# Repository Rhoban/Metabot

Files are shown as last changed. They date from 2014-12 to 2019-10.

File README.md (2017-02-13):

# The Metabot open-source quadruped robot

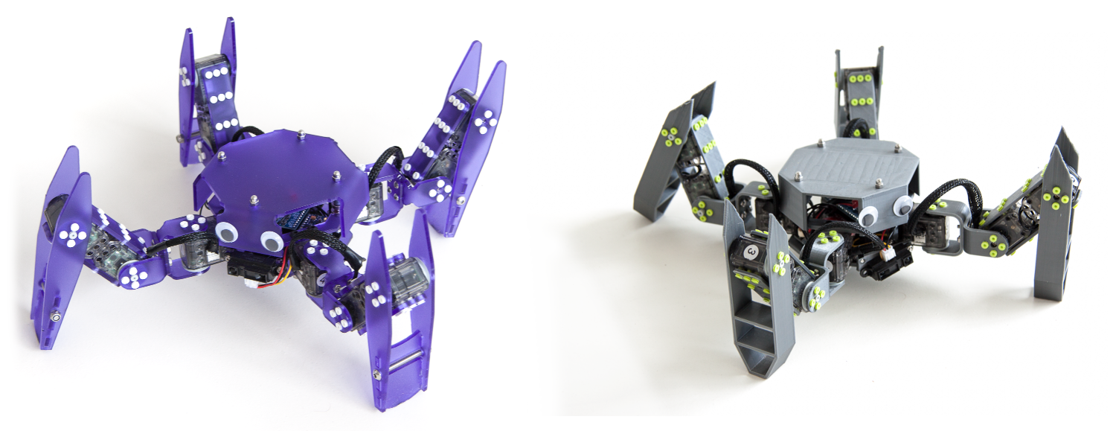
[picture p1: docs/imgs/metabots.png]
Metabot


Metabot is an open-source DIY quadruped robotics platform. It can be 3D printed or
laser cutted (3mm acrylic).

Note that [the robot is now available as a kit](http://metabot.cc).
In this repository you will find all the open-source material to make (or hack) your own.

* [Bill of material](docs/bom.md)
* Mechanics
    * [3D Parts](mechanics/3d)
    * [Laser parts](mechanics/laser)
* [Electronics](electronics)
* [Firmware](firmware)
* [Joypad firmware](dfpad)

You can control the robot using the Metabot app (available on the Play Store)

[To get information about the previous robot version, see branch V1](https://github.com/Rhoban/Metabot/tree/v1)

## License

This project is under CC BY-NC license:
http://creativecommons.org/licenses/by-nc/3.0/

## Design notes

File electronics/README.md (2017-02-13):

# Metabot electronics

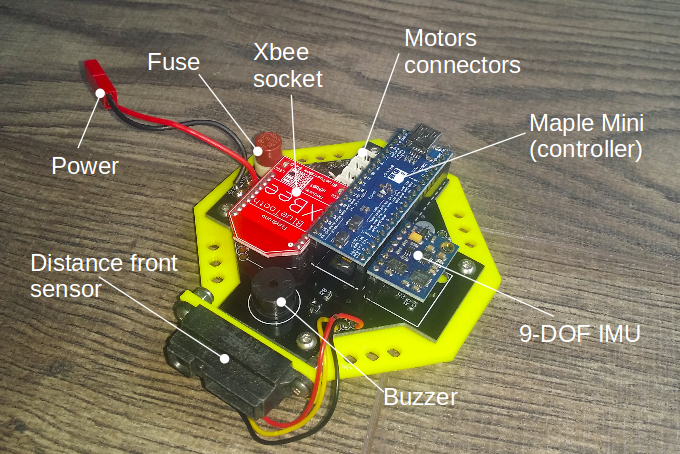
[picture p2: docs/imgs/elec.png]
Electronics


Here are eagle schematics of the XBoard, the electronics inside the Metabot
robot.

## BOM

To assemble the board, you'll need the following components:

Name       | Farnell       | Quantity      | Description
-----------|---------------|---------------|--------------------------------------
MOLEX-53253-0370 | 1756921 | 4 | Connector for the motors
CD74HCT367M | 1739593 | 1 | Bus driver
1x20 0.1" header | 1593469 | 2 | Connector for the maple mini
1x8 0.1" header | 1593463 | 1 | Connector for the IMU
1x10 1mm header | 1109732 | 2 | Connector for the XBee
CEM-1203 | - | 1 | Buzzer
BC817 | 1081223RL | 1 | NPN transistor for the buzzer
EEE1CA470SP | 9696946 | 1 | 47uF decoupling capacitor
EEEFK1C221XP | 1850103 | 1 | 220uF decoupling capacitor
TS2940CW-3.3RP | 7261403RL | 1             | 3.3V Regulator
AP1117E50G-13 | 1825292RL  | 1             | 5V Regulator
LITTELFUSE  56000001009  | 1185363 | 1     | Fuse holder
Radial Fuse, 3.15A  37013150410 | 1716619 | 1 | Fuse
SUD50N04-8M8P-4GE3 | 1794799 | 1     | This big MOS can blow up the fuse programmatically
JST-BEC connector | - | 1 | Connector for the battery
R0805 22 ohms | - | 2 | 
R0805 470 ohms | - | 2 | 
R0805 1 Kohms | - | 1 |
R0805 4 Kohms | - | 3 |
R0805 10 Kohms | - | 1 |
R0805 20 Kohms | - | 1 |
C0805 100nF | - | 1 |

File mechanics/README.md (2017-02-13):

# Mechanics

Here are the mechanics parts, [documentation can be found here](/doc/bom.md)

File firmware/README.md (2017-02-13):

# Firmware

The firmware is the code that is loaded on the robot and that generates the
walking gait and talks to the motors. It is currently only adapted for the
original 12-dof Metabot (4 legs, 3 motors per leg).

## Putting the firmware on the robot

### Linux

You need to install the following packets:

```
$ apt-get install python python-serial
```

To put the firmware on the robot, simply cd into the `firmware/` repository and
run the installation script:

```
sudo python robotis-loader.py /dev/ttyACM0 metabot2.bin
```

This should reset the board and then output some progress bar, your firmware is now
on the robot!

### Windows

You'll need python and pyserial. Then, be sure to have the drivers. You can install
simply OpenCM IDE for that.

Then, run:

```
sudo python robotis-loader.py COM4 metabot2.bin
```

Replace COM4 with the right serial port (you can see it in OpenCM ide or in the devices
manager).

## The terminal

### Connecting to the on-board terminal

#### Linux

You can open a serial connection with the robot using `cu` or `screen`. You can use
for instance:

```
you@yourmachine: cu -l /dev/ttyACM0
Connected.

$  
```

Type "~." to quit cu.

#### Windows

On Windows, you can use a serial client such as PuTTy. Just choose "Serial" as connection
mode and enter "COMx", where x is the number of the device.

You can find the number of the device in the devices manager.

## Commands

### Basics

#### `start`: Enable the motors

This will enable the motors. The LEDs will turn green and the torque will rise
slowly until the robot reaches it default position.

#### `stop`: Stop the motors

Turns the LEDs red and shuts the torque down.

#### `beep [freq] [duration]`: Emit a beep

This will emit a beep using the internal buzzer, using `freq` Hz and `duration`
ms.

### Controller

Here are commands that can be used to control the motion of the robot

#### `dx`, `dy`, `turn`: Controls the robot

These are parameters that control the robot speed. Actually, `dx` and `dy`
control the size of the each step (in mm) and `turn` the angle of each step
(in °).

#### `freq`: Steps per second

This is the number of step the robot does on each second.

#### `h`: Robot height

This is the (z, in mm) height of the robot while it walks.

#### `r`: Radius

This is the radius of the legs (in mm), i.e the distance of the legs to the
center of the body while walking.

#### `alt`: Legs altitude

This parameters controls the height the legs are lifted up (in mm) while
walking.

#### `crab`: Crab position

This is an angle (in °) that can be positive or negative and allows to get a
crab-like position while walking.

## Building, developing & hacking the firmware

See the [firmware source README](src#firmware-source)

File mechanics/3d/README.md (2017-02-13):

# Mechanics

Here are the 3D mechanics parts, [documentation can be found here](/docs/bom.md)

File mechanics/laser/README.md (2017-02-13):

# Mechanics

Here are the laser mechanics parts, [documentation can be found here](/docs/bom.md)

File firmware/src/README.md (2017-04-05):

# Firmware source

## Building, developing & hacking the firmware

See the [firmware source](src/README.md)

You should install the arm cross-compilation toolchain:

```
sudo apt-get install libstdc++-arm-none-eabi-newlib gcc-arm-none-eabi libnewlib-arm-none-eabi binutils-arm-none-eabi
```

The firmware source is in the `src/` directory. To build it, you'll first have to run the
prepare script to get the Maple framework:

```
./prepare.sh
```

Then, run `make`:

```
make
```

You can use `make install` to send directly the firmware on the robot:

```
make install
```

## Creating behaviors

We already designed a simple architecture with few examples that can be found in the
firmware in order to create behaviors for the robot.

First, edit `behavior.h` and change the `BEHAVIOR_ENABLE` constant to `1`. Then, edit
`behavior.cpp`, you can read the examples functions and uncomment the one(s) you like
in the `behavior_tick` method.

This will be executed when the robot is started (i.e when the `start` command is sent and
after the motors are enabled). Feel free to edit this to create your own, custom behavior.

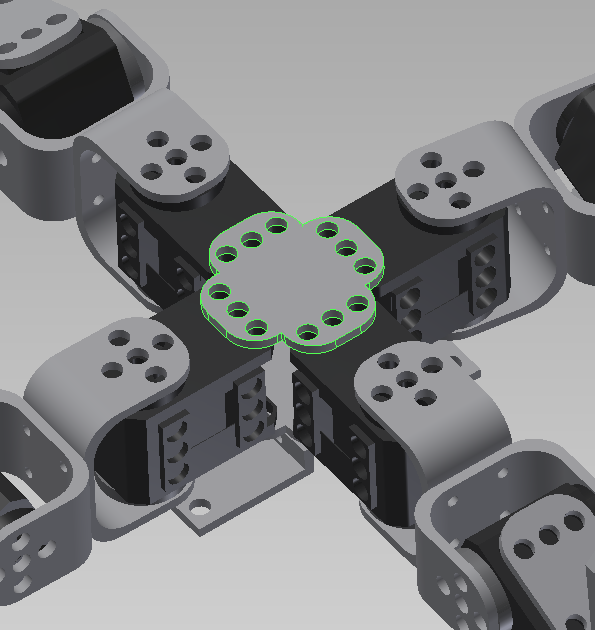
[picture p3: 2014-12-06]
mechanics/3d/imgs/body.png

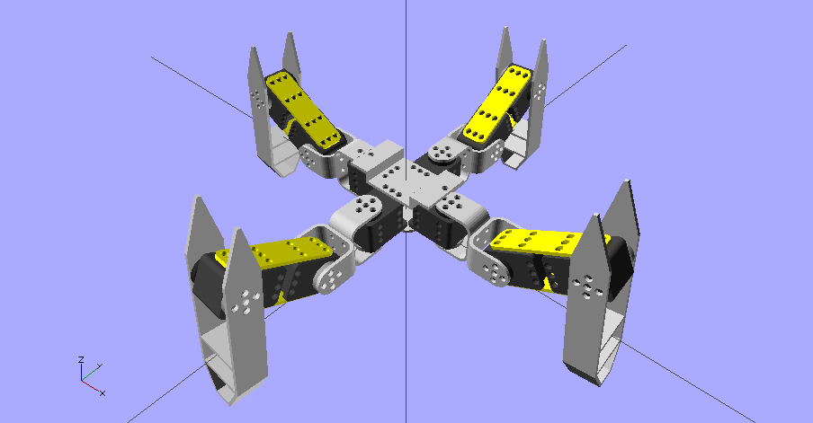
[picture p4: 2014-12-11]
mechanics/3d/imgs/side.png

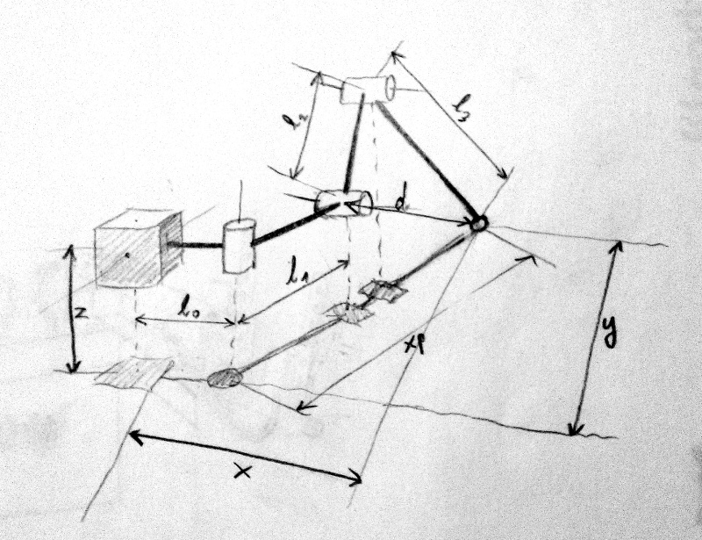
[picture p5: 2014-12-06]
docs/imgs/kinematic.jpg

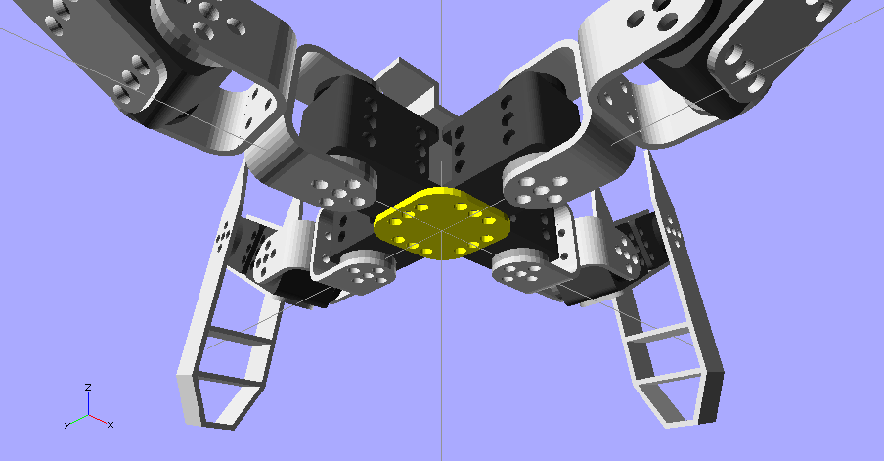
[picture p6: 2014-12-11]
mechanics/3d/imgs/body_bottom.png

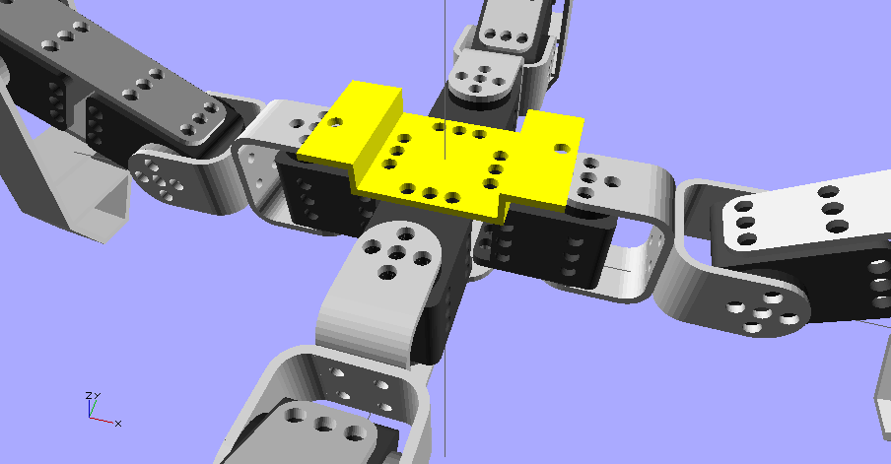
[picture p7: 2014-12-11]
mechanics/3d/imgs/body_top.png

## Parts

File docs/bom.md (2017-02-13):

# Bill of material

Metabot V2 bill of materials

## ROBOTIS parts

Name                   | Quantity | Description                  
-----------------------|----------|----------------------------------
XL-320                 | 12       | Robot servo-motors
Short Rivets           | ~300     | Short rivets
Long Rivets            | 48       | Long rivets
Ollo Pulley            | 12       | The pulley for the counter-axis
Ollo Tool              | 1        | A plastic tool that can be used to handle rivets

## Electronics

Name                   | Quantity | Description                  
-----------------------|----------|----------------------------------
XBoard                 | 1        | This is the custom [board](/electronics/) of the robot
Maple Mini             | 1        | A controller featuring a STM32F103CBT6, with sockets
Mini USB cable         | 1        | You'll need it to connect to the Maple Mini
GY-85 IMU              | 1        | 9DOF inertial measurement units (accelerometer, gyroscope and magnetometer)
XBee Bluetooth         | 1        | You can actually choose any bluetooth chip you want
GP2Y0A21YK             | 1        | 10 to 80 cm infrared distance sensor

## Batteries

The XBoard features a JST-BEC female connector, which is compatible with many LiPo battery.
You can actually use a lot of different power sources, but we recommend you the following references:

Name                   | Quantity | Description                  
-----------------------|----------|----------------------------------
1000mAh 2S (7.4) LiPo  | 1        | A battery, be careful about its geometry
IMAX B3 AC charger     | 1        | A cheap and simple to use LiPo charger

## Mechanics

Name                   | Quantity | Description                  
-----------------------|----------|----------------------------------
M4x40                  | 12        | Tie the leg tips and the body
M3x8                   | 7        | 4 for the magnets to the head, 1 for the IMU and 2 for the GP-2
M3x5 (countersunk)     | 4        | Used to tie the magnets to the spacers
M3 nylstop caps        | 16       | We recommend nylstop caps
M4 nylstop caps        | 12       | We recommend nylstop caps
M3 blind cap nut       | 4        | Blind caps are prettiest for the top of the head
Nylon M3 cap           | 17       | 8 for the electronics, 1 for the IMU, 2 for the GP-2, 4 for the body spacers, 2 to replace magnets (to avoid magnetic interference)
M3x12 male spacer      | 1        | For the IMU
M3x15ish male spacer      | 4        | For the electronics
M3x10                  | 20        | 16 for the Us, 4 for the electronics 
Countersunk magnet (10x3mm, 3mm hole) | 6        | To plug and unplug the head
Googly eyes            | 2        | You can paste it on the front on the robot to get it nicer

Note that you'll need allen 2 and 2.5, and a flat plier or an hex wrench for the nylstop caps

## Parts

For mechanical parts, you have choice between 3D and laser. You can either print the
parts yourself or cut it and bend it.

### The 3D option

Name                   | Quantity 
-----------------------|----------
[U](/mechanics/3d/u.stl) | 8      
[side](/mechanics/3d/side.stl) | 8
[leg](/mechanics/3d/leg.stl) | 4
[body_bottom](/mechanics/3d/body_bottom.stl) | 1
[body_top](/mechanics/3d/body_top.stl) | 1
[head](/mechanics/3d/head.stl) | 1

### The laser option

The parts are provided as DXF, the black layer (0) is cutting and the red one (1)
is 1mm engraving. The target material is 3mm thick PMMA (acrylic).

A packet version can also be [found here](/mechanics/laser/metabot.dxf).

Name                   | Quantity | Comment
-----------------------|----------|-------------
[U](/mechanics/laser/parts/u.dxf) | 8 | [Requires bending](/mechanics/laser/doc/u_bending.pdf)
[side](/mechanics/laser/parts/side.dxf) | 8 | 
[leg](/mechanics/laser/parts/leg.dxf) | 4 |
[tip](/mechanics/laser/parts/tip.dxf) | 4 |
[tip_up](/mechanics/laser/parts/tip_up.dxf) | 4 |
[body_bottom](/mechanics/laser/parts/body_bottom.dxf) | 1 | [Requires bending](/mechanics/laser/doc/body_bending.pdf)
[body_top](/mechanics/laser/parts/body_top.dxf) | 1
[head](/mechanics/laser/parts/head.dxf) | 1 | [Required bending](/mechanics/laser/doc/head_bending.pdf)

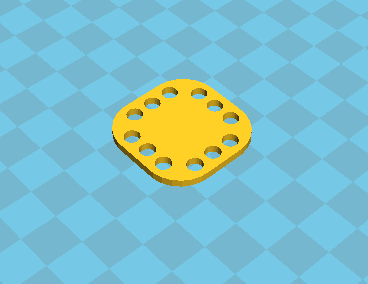
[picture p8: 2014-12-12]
mechanics/3d/imgs/parts/body_bottom.png

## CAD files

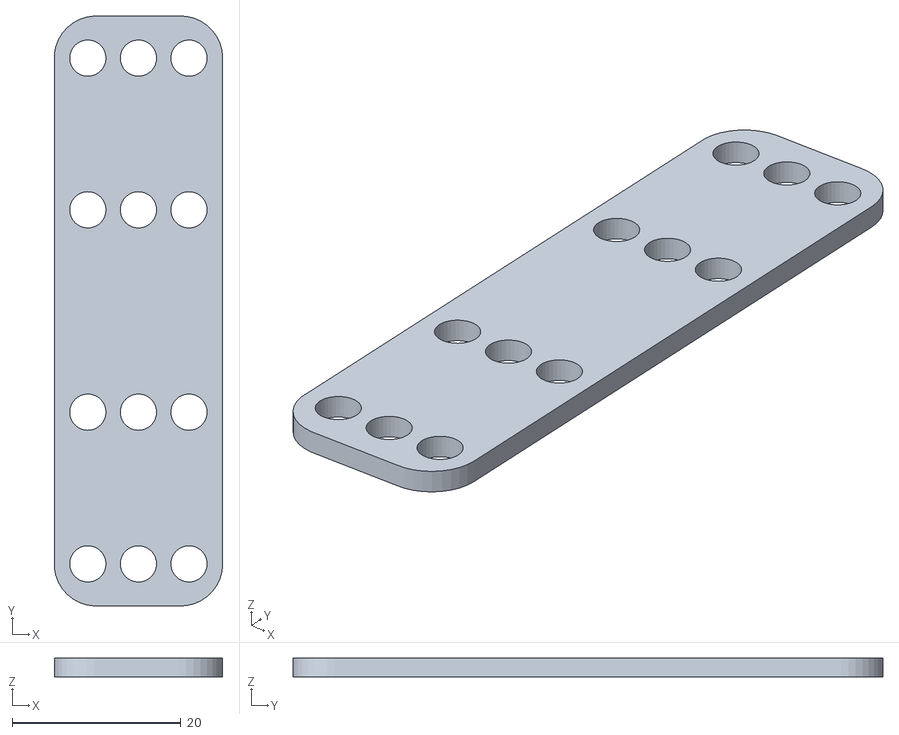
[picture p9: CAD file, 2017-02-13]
mechanics/3d/side.stl
20.0 x 70.0 x 2.20

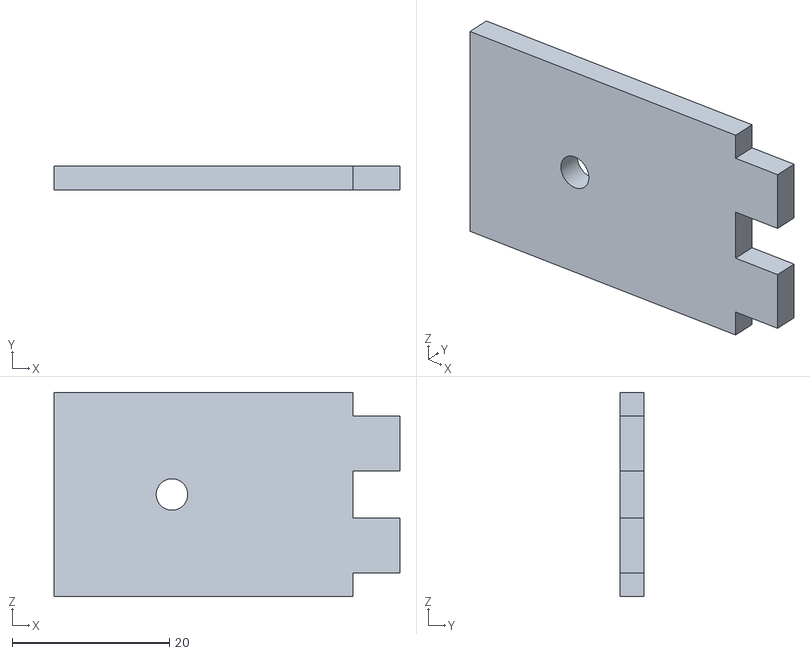
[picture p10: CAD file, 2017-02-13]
mechanics/laser/autodesk/u_pattern/u_side.stl
44.0 x 3.00 x 26.0

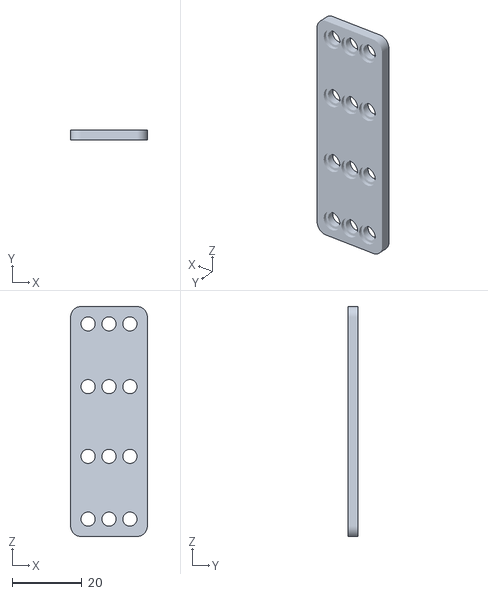
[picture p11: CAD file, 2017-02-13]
mechanics/laser/side.stl
22.0 x 3.00 x 66.0

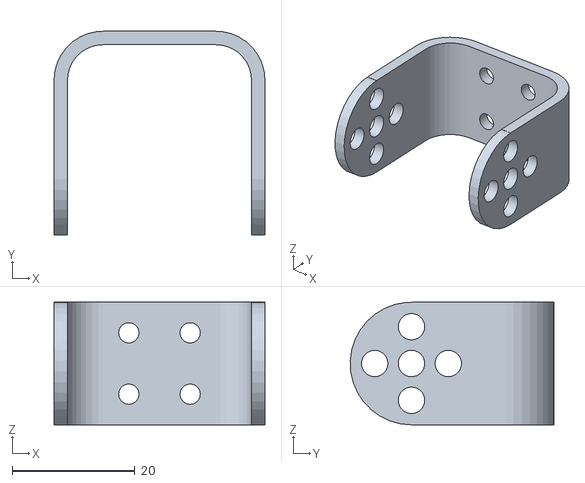
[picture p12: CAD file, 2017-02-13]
mechanics/3d/u.stl
34.4 x 33.2 x 20.0

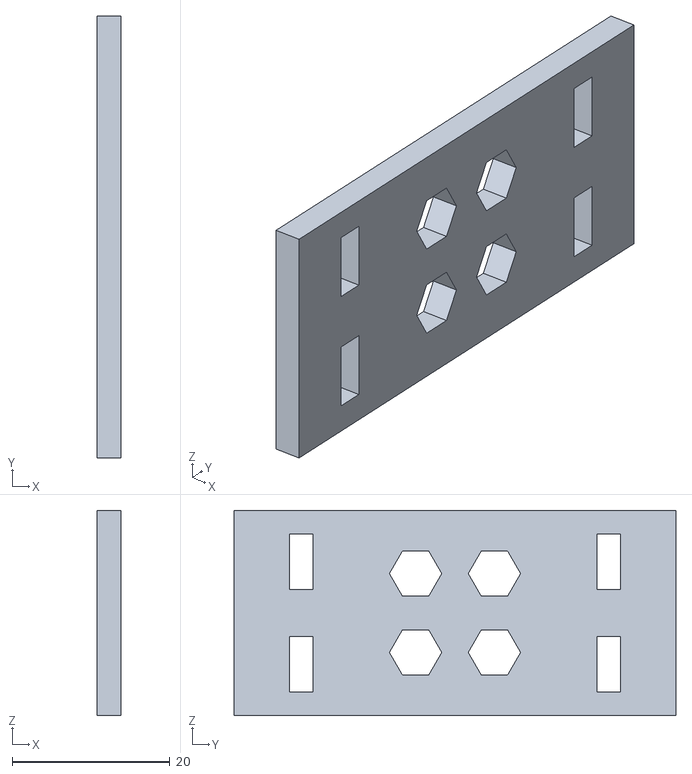
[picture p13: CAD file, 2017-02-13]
mechanics/laser/autodesk/u_pattern/u_base_hex.stl
3.00 x 56.0 x 26.0

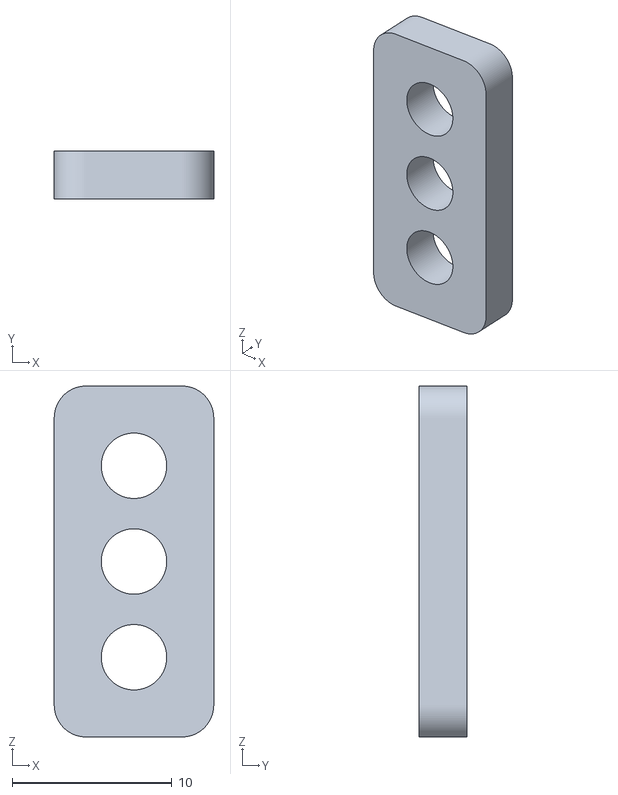
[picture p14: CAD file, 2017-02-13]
mechanics/laser/spacer.stl
10.0 x 3.00 x 22.0

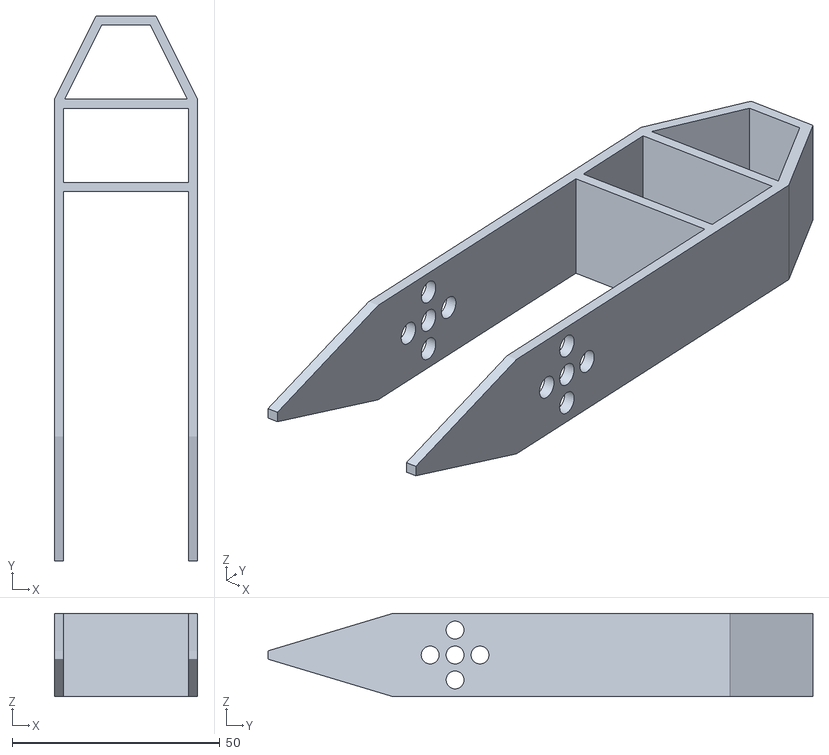
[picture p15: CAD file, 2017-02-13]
mechanics/3d/leg.stl
34.4 x 131.1 x 20.0

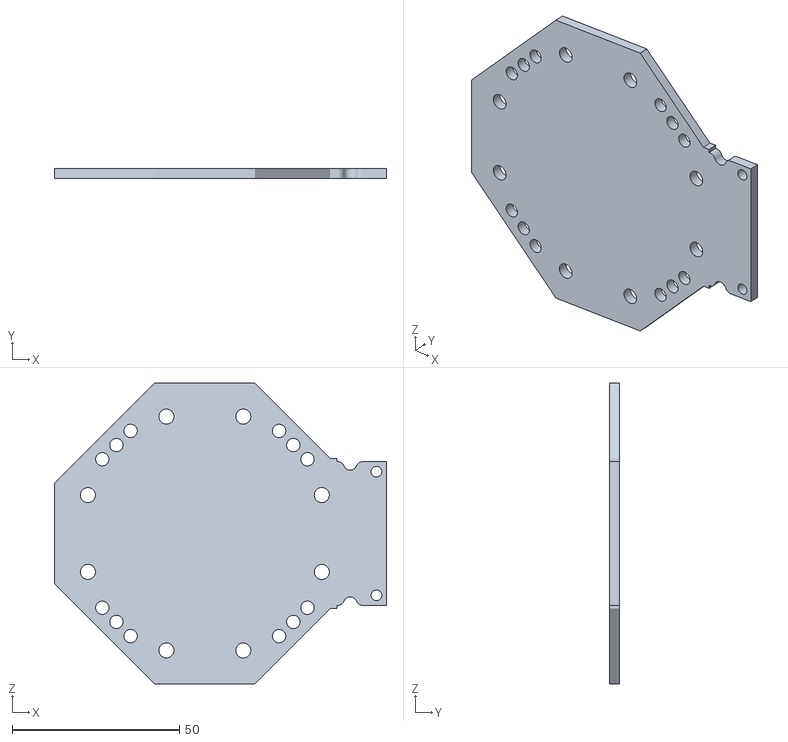
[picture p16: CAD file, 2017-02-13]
mechanics/laser/body_bottom.stl
99.4 x 3.00 x 90.0

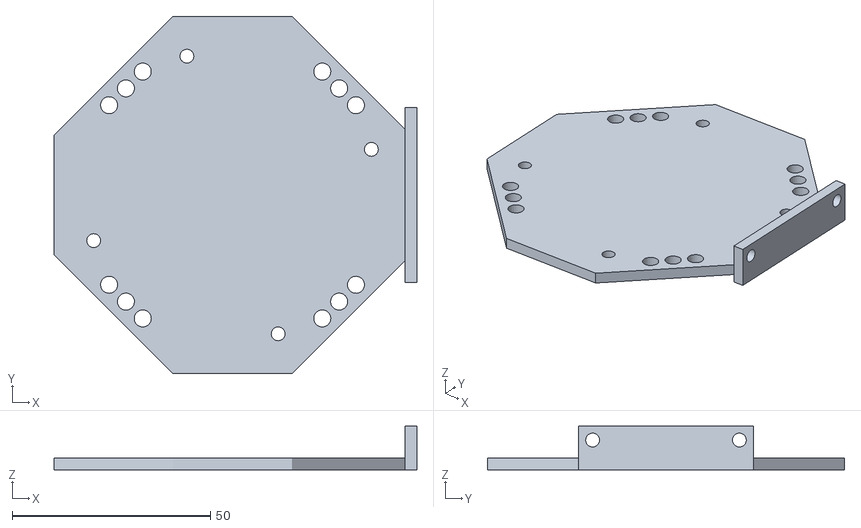
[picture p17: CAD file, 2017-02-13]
mechanics/3d/body_bottom.stl
91.5 x 90.0 x 11.0

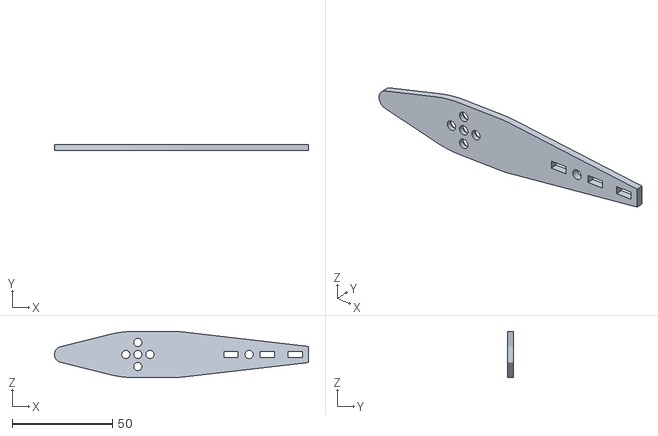
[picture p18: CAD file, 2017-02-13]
mechanics/laser/leg.stl
126.5 x 3.00 x 23.0

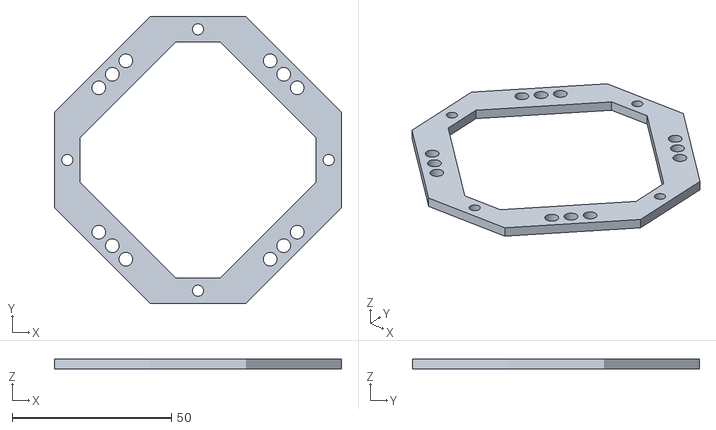
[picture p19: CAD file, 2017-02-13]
mechanics/3d/body_top.stl
90.0 x 90.0 x 3.00

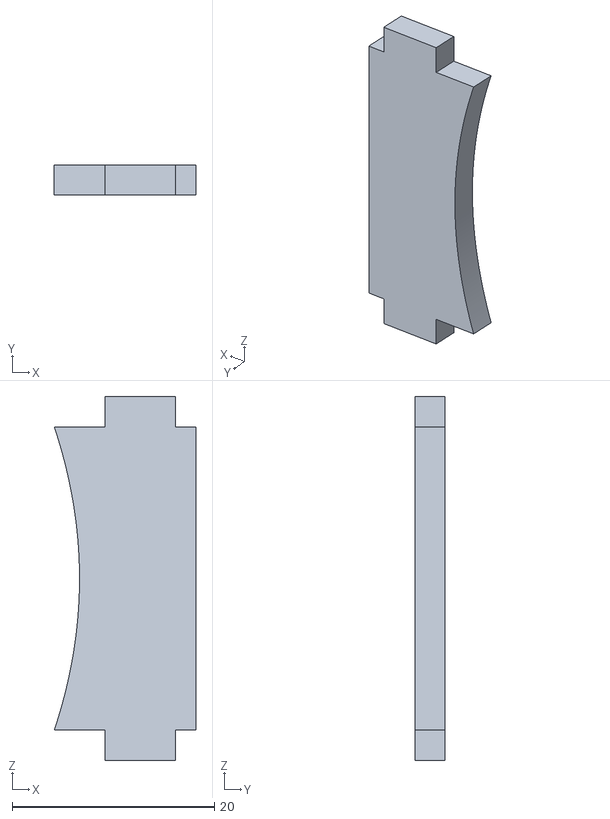
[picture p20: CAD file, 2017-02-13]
mechanics/laser/tip_up.stl
14.0 x 3.00 x 36.0

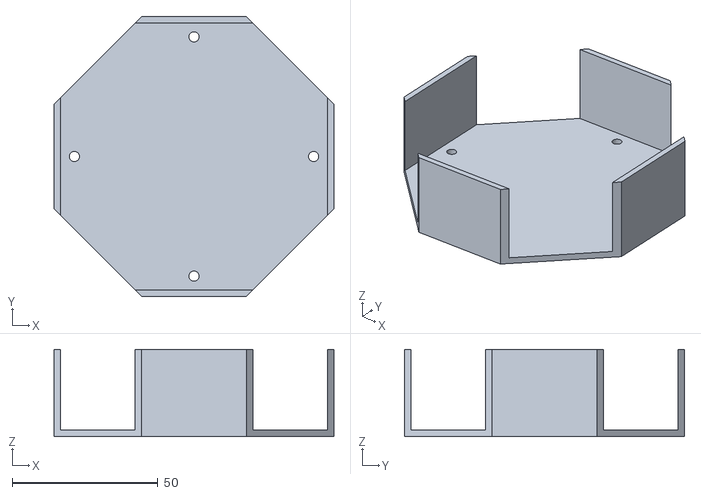
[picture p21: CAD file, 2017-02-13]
mechanics/3d/head.stl
96.0 x 96.0 x 30.0

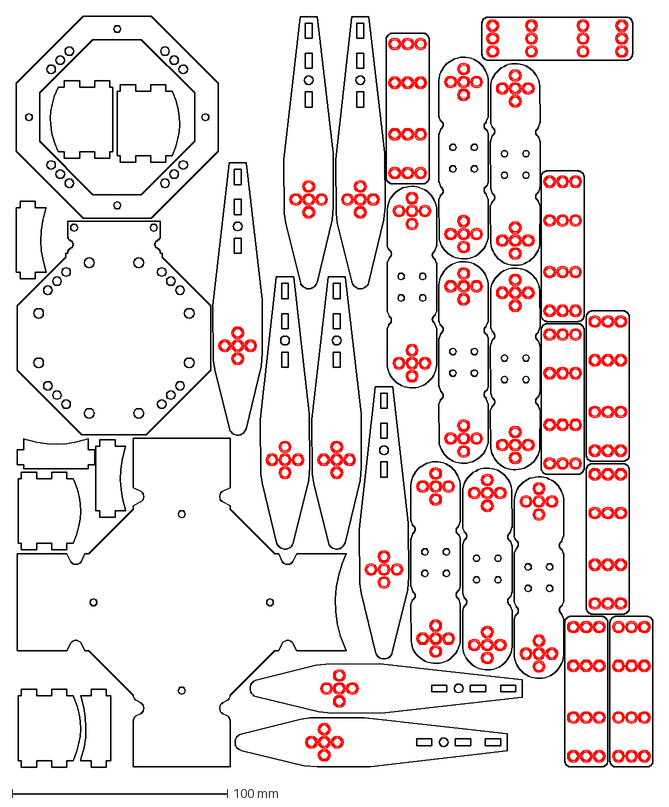
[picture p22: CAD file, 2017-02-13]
mechanics/laser/metabot.dxf
296.0 x 349.0 mm

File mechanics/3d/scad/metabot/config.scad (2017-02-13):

// Color of the parts, for rendering
PartsColor = [0.8, 0.8, 0.8];

// Head height
HeadHeight=30;

// Thickness of parts (2.2 is good for Ollo rivets)
Thickness = 2.2;
BodyThickness = 3;

// Sizes of the parts of the leg
// Ratio of leg parts
LegSize = 100;
LegSizeA = (0.60)*LegSize;
LegSizeB = (0.20)*LegSize;
LegSizeC = (0.20)*LegSize;

// Width of the bottom part of the leg
LegSizeBottom = 10;

// Size of the "top" part of the legs, in mm
LegSizeTop = 30;

// Motor dimensions
MotorWidth = 24;
MotorHeight = 36;
MotorDepth = 24;
MotorArmOffset = 9;

// U dimensions
UHeight = 15.2;
URadius = 8;
UWidth = 30+Thickness/2;
UTotalHeight = UHeight+URadius;
UScrewsSpacing = 10;
UScrewsDiameter= 3.3;

// Side dimensions
SideSize = 35;
SideHolesToBorder = 5;

// Defining the resolution
$fn=35;

module metabot_colorize() {
    color(PartsColor)
        children();
}

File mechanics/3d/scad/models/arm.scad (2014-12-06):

include <ollo.scad>;

module arm(counter=false) {
    c = counter?[0.6,0.6,0.6]:[0.15,0.15,0.15];
    color(c) {
        difference() {
            cylinder(d=20, h=OlloWidth);
            servoArm(OlloWidth);
        }
    }
}

arm();

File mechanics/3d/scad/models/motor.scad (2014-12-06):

include <ollo.scad>;
use <../util/rounded.scad>;

// Motor dimensions
MotorWidth = 24; 
MotorHeight = 36; 
MotorDepth = 24; 
MotorArmOffset = 9;

module motor(width=2.2) {
  translate([0,-MotorArmOffset,-MotorDepth/2]) {
  color([0.25,0.25,0.25]) {
	 difference() {
  	   rounded(MotorWidth,MotorHeight,MotorDepth,3,center=true);

		// Bottom
      translate([-MotorWidth/2-0.1,-MotorHeight/2-0.1,3])
	     cube([MotorWidth+0.2, 5.7, MotorDepth-6]);

		translate([0,-MotorHeight/2+3])
		  threeOllo(MotorDepth);

		// Motor shaft
	   translate([0, MotorArmOffset])
     	  olloHole(MotorDepth+5);

		// Side holes
		for (side=[-MotorWidth/2,MotorWidth/2-width]) {
		translate([side,9,MotorDepth/2]) {
		  rotate([0,90,0]) {
		   threeOllo();
			translate([0,-3*OlloSpacing,0])
			  threeOllo();
		  }
		}
		}
	 }
  }
	}
}

motor();

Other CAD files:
mechanics/laser/autodesk/robot.dwg
mechanics/laser/autodesk/u_pattern/u_base.stl
mechanics/laser/u.stl
mechanics/laser/head.stl
mechanics/3d/scad/models/motor_arm.scad
mechanics/3d/scad/joints/double_u.scad
mechanics/3d/scad/joints/side_to_side.scad
mechanics/3d/scad/metabot/joints.scad
mechanics/3d/scad/metabot/metabot.scad
mechanics/3d/scad/metabot/parts.scad
mechanics/3d/scad/metabot/print/body_bottom.scad
mechanics/3d/scad/metabot/print/body_projection.scad
mechanics/3d/scad/metabot/print/body_top.scad
mechanics/3d/scad/metabot/print/head.scad
mechanics/3d/scad/metabot/print/leg.scad
mechanics/3d/scad/metabot/print/leg_projection.scad
mechanics/3d/scad/metabot/print/side.scad
mechanics/3d/scad/metabot/print/side_projection.scad
mechanics/3d/scad/metabot/print/u.scad
mechanics/3d/scad/metabot/print/u_projection.scad
mechanics/3d/scad/models/ollo.scad
mechanics/3d/scad/parts/body.scad
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

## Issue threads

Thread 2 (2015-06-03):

bug de simulateur

theking391, 2015-06-03:
le simulateur ne me permet pas d'effectuer un rectangle de 1200 mm sur 2200mm . Le robot ne respecte pas les angles imposés il dévie de sa trajectoire a partir du second coté ( le 1er 22000mm)

Gregwar, 2015-06-03:
Bonjour,
Les trajectoires simulées ne sont en effet pas parfaites, mais cela sera encore pire dans la réalité
Le robot va glisser sur le sol, les moteurs auront du retard etc.

theking391, 2015-06-03:
c'est embêtant car je dois participer a un concours et si je ne peux pas m'entrainer sur le logiciel ni sur le robot cela me désavantage grandement .Auriez vous une astuce/idée de comment résoudre ce problèmes ??

Gregwar, 2015-06-03:
Vous ne devez de toutes façon pas miser sur le fait qur les trajectoires seront suivies parfaitement
Essayez de fermer les yeux et de faire un parcours: c'est le même probleproblème

theking391, 2015-06-03:
ah. alors on va essayer de se débrouiller merci pour les infos:)

Gregwar, 2015-06-03:
Avez vous vu la vidéo de tutoriel?

alexandremrnd, 2015-06-03:
Bonjour,
Je suis un ami de theking391 et nous travaillons ensemble sur ce projet et je vous confirme que nous avons regarder la vidéo de tutoriel mais même en suivant toutes les étapes notre carré ou rectangle (de n'importe quelle taille d'ailleurs) ne respecte pas les angles et les rend inférieurs à 90°.
 Merci à vous :)

Gregwar, 2015-06-03:
Ce qu'il faut savoir, c'est que le robot fait des mouvements qui devraient *théoriquement* donner 90° ou tant de milimètres, mais dans la pratique, un grand nombre de choses peuvent faire que ça ne marche pas
Il est impossible de faire des "parcours" précis sans capteurs (dans une prochaine version, le robot sera équipé de capteurs de distances) ni aucun retour d'information
C'est un peu comme si vous essayiez de faire un parcours les yeux fermés

alexandremrnd, 2015-06-04:
Merci à vous pour votre suivi de notre problème. Pour information, nous travaillons avec Madame Blanc pour le Robot Maker's Day.
A bientôt. :)

Closed 2015-12-14.

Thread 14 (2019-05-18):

build error

leelegend94, 2019-05-18:
Compiling failed while "[LD]        maple_mini.elf" with many errors like the followings:

build/./Maple/LibRhoban/commands.o: In function `start()':
/home/parallels/Workspace/rl/metabot_project/firmware/src/Maple/LibRhoban/commands.cpp:69: undefined reference to `dxl_flush()'
...

AndreasFWallin, 2019-05-29:
I have the same problem, both on Windows and Linux

leelegend94, 2019-06-05:
There are 2 source file not compiled by default, which is however crucial for Metabot...
Fix:
in firmware/src/Maple/LibRhoban/rules.mk
1. "ENABLE_DXL := no"  --> "ENABLE_DXL := yes"
2. uncomment "#cppSRCS_$(d) += servos.cpp"
3. have fun

Closed 2019-06-05.

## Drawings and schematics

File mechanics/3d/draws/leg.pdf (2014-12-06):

11

22

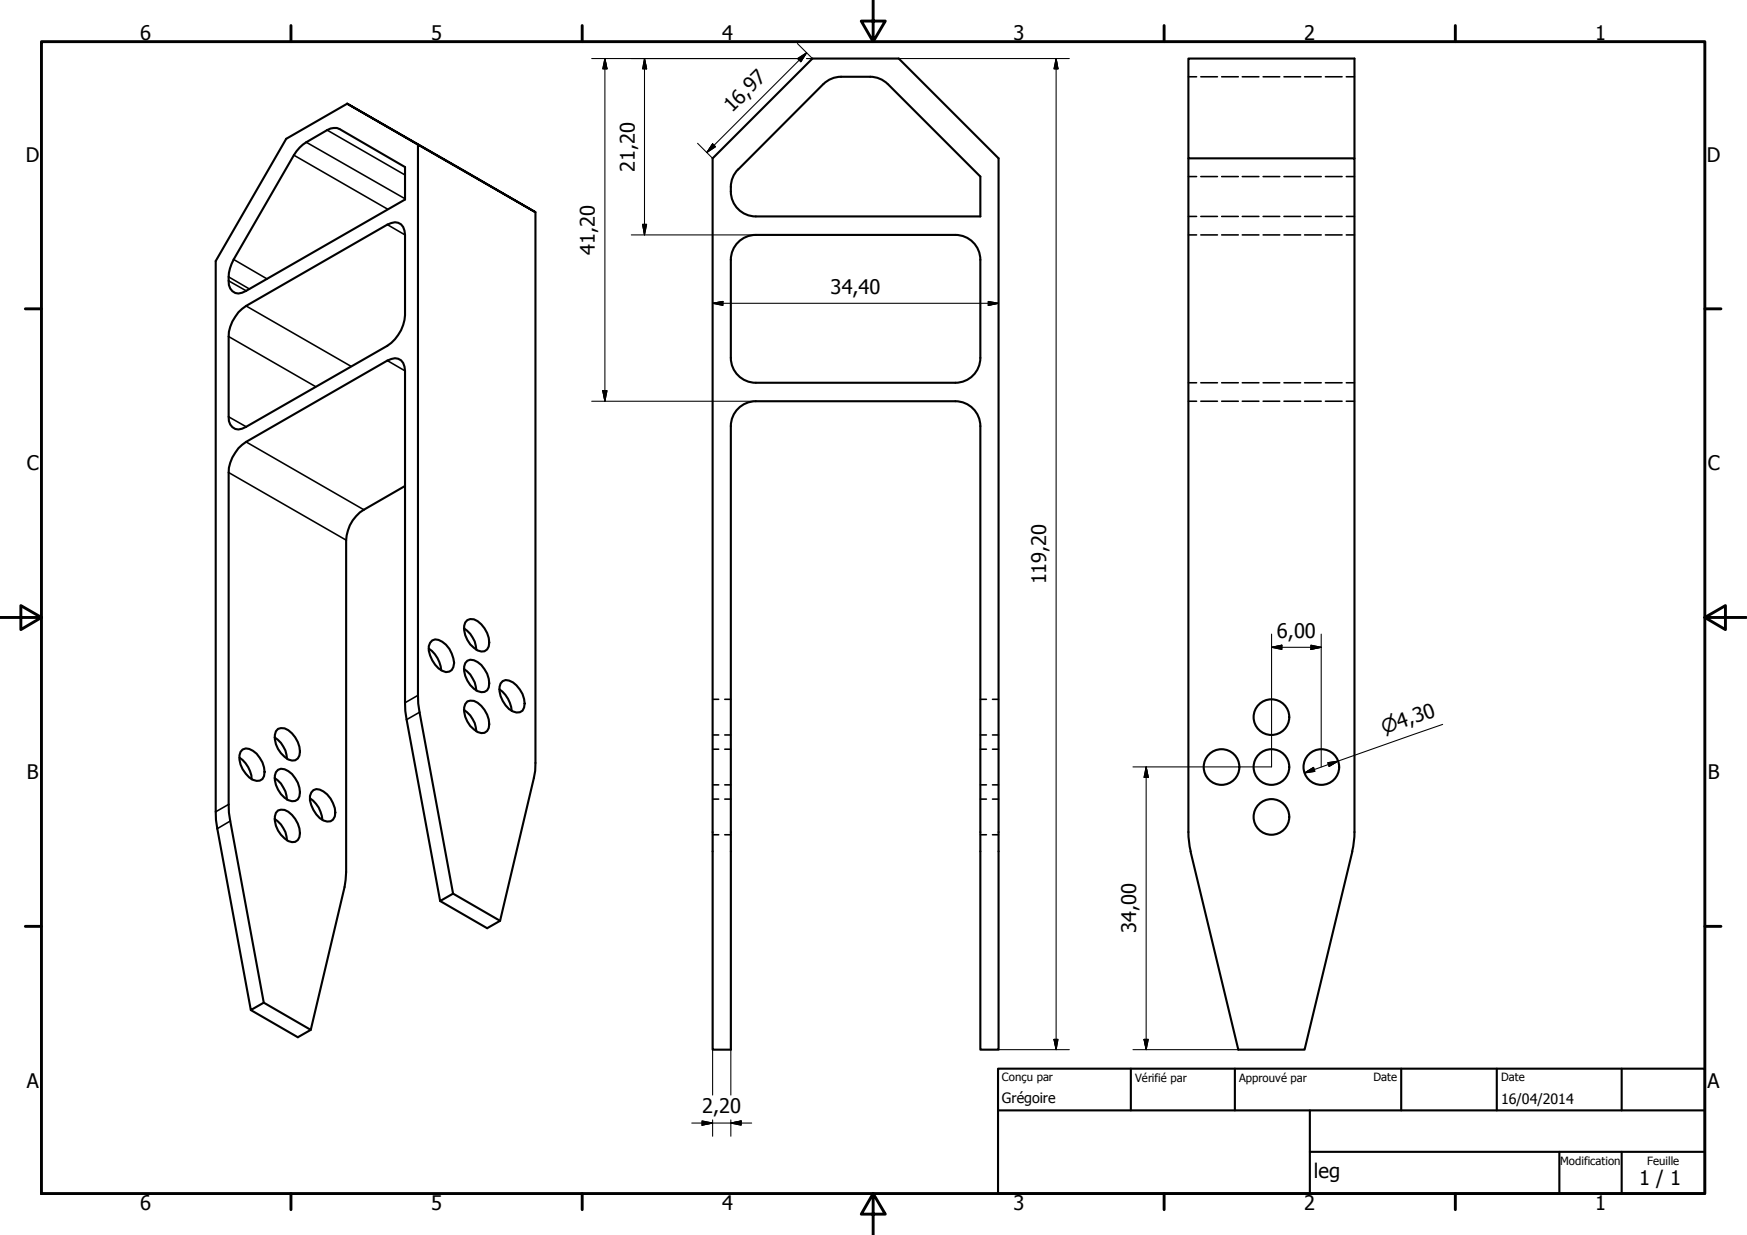
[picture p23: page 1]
D leg; ille

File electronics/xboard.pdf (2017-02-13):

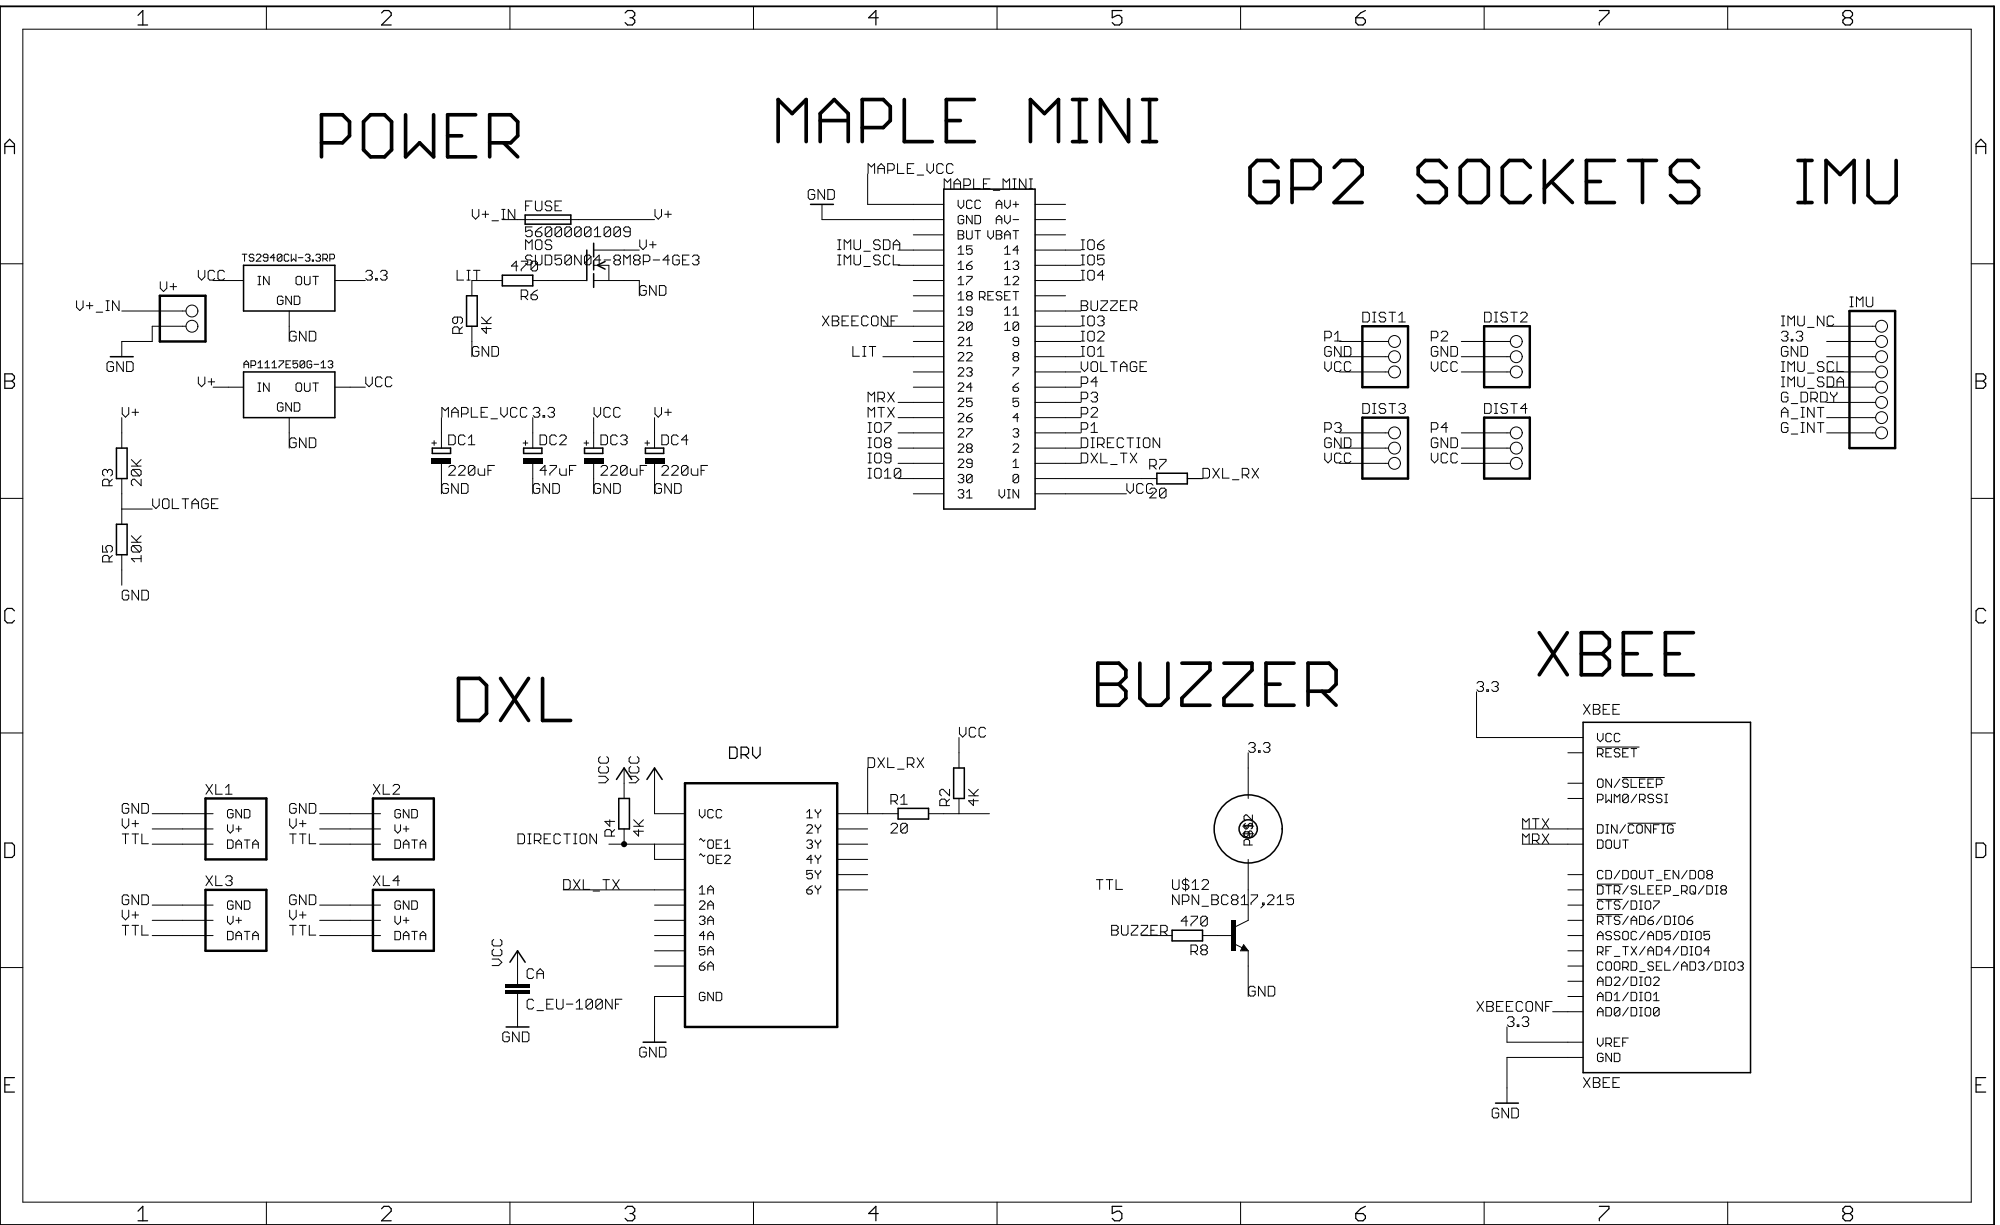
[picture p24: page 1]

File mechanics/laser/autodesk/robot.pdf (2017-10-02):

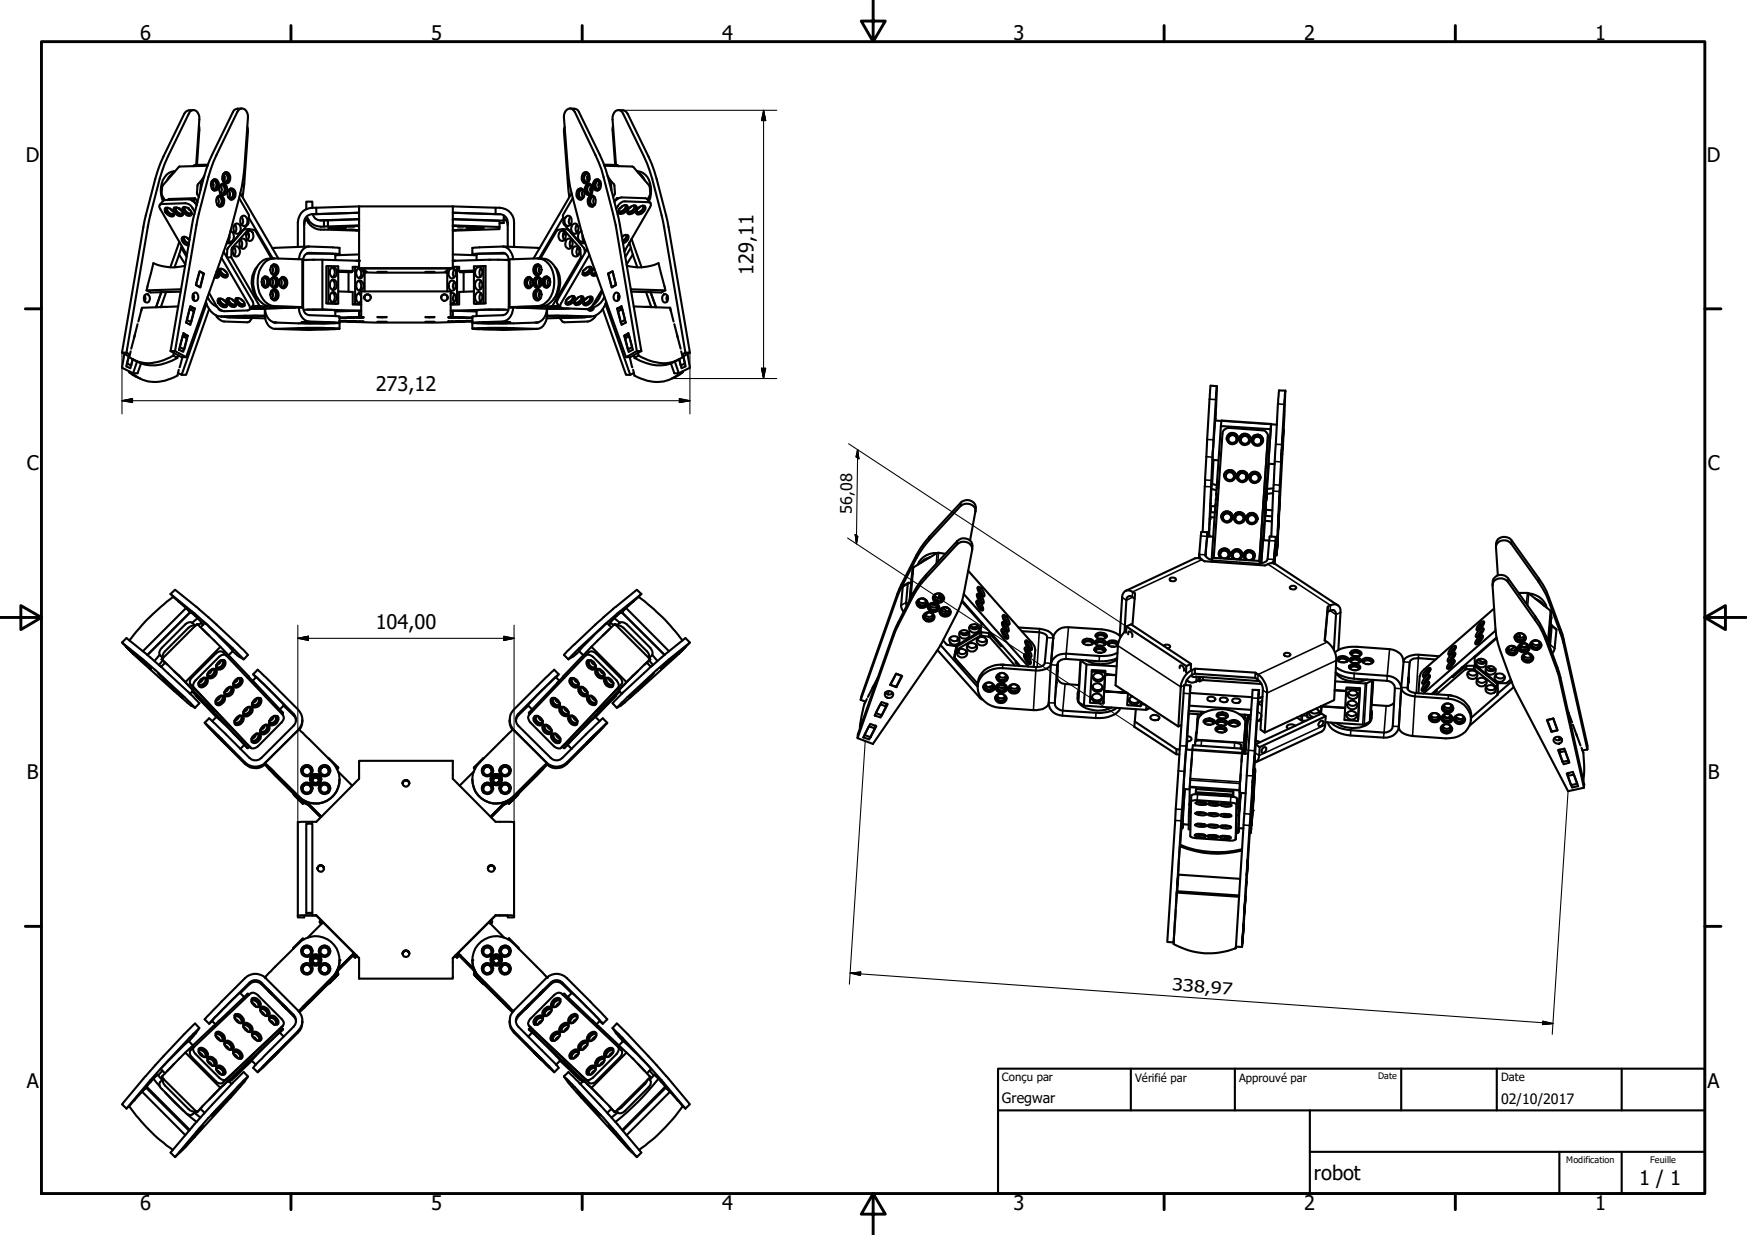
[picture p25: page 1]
robot; Gregwar; Conou par; Vprifip par; Approuvp par; Date; Modification; Feuille

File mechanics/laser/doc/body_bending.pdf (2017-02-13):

1

2

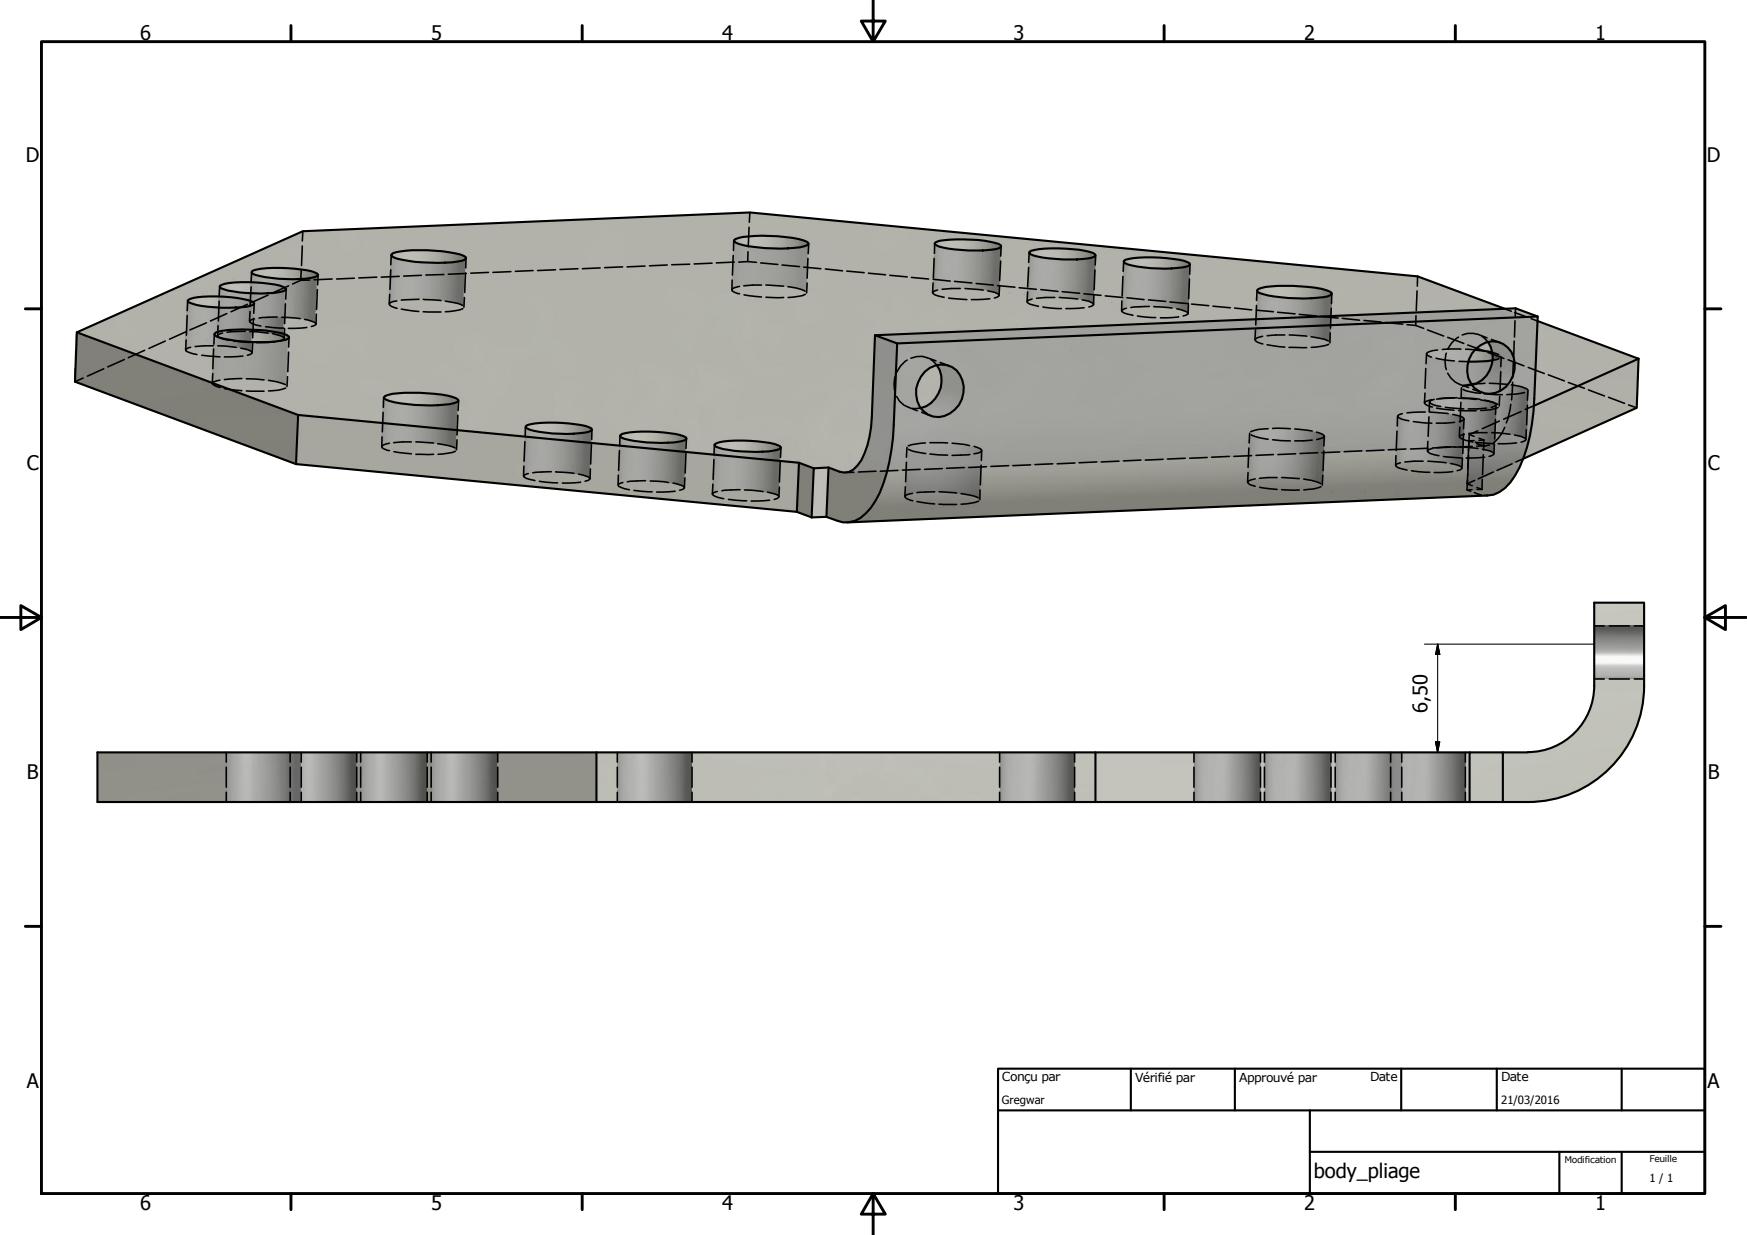
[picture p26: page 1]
body_pliage; Gregwar; Conou par; Vprifip par; Approuvp par; Date; Modification; Feuille

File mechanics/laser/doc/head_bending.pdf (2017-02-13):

1

2

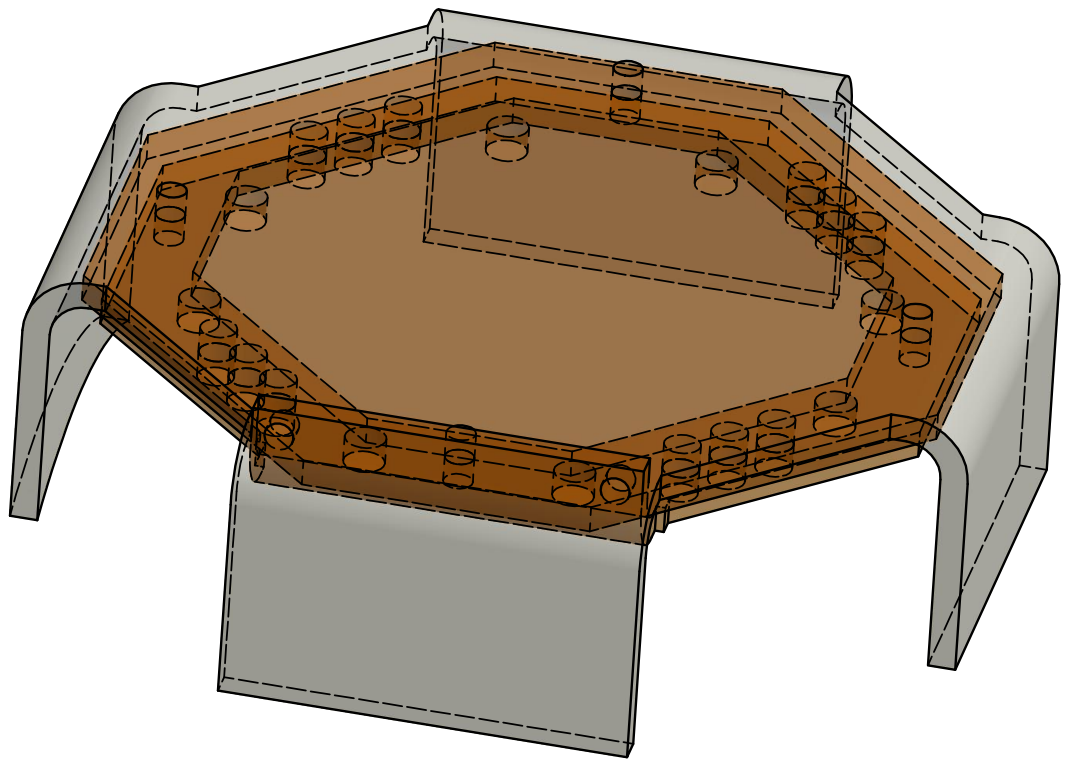
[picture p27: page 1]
Gregwar; Conou par; Vprifip par; Approuvp par; Date; Modification; Feuille

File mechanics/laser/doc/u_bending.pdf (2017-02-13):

1

2

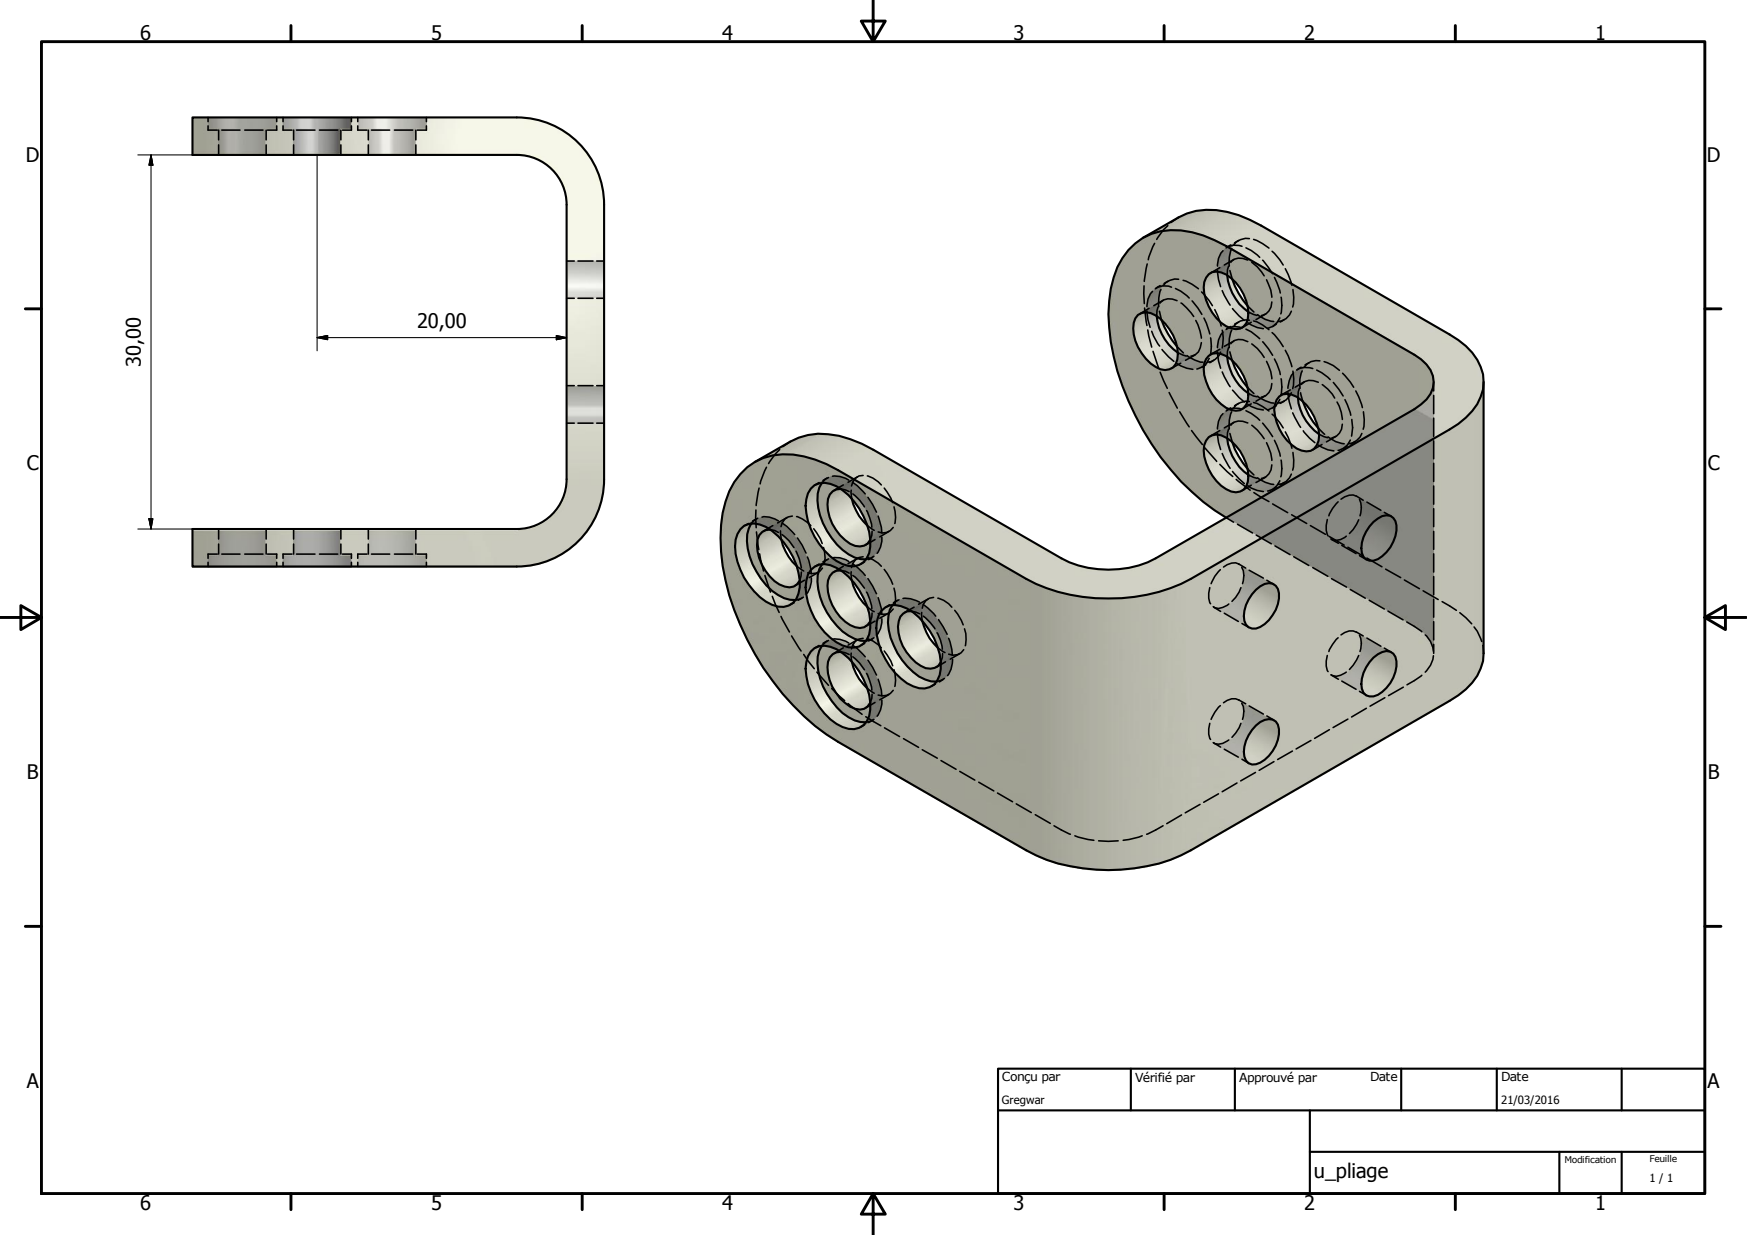
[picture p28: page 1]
u_pliage; Gregwar; Conou par; Vprifip par; Approuvp par; Date; Modification; Feuille

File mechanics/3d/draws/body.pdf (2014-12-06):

1

2

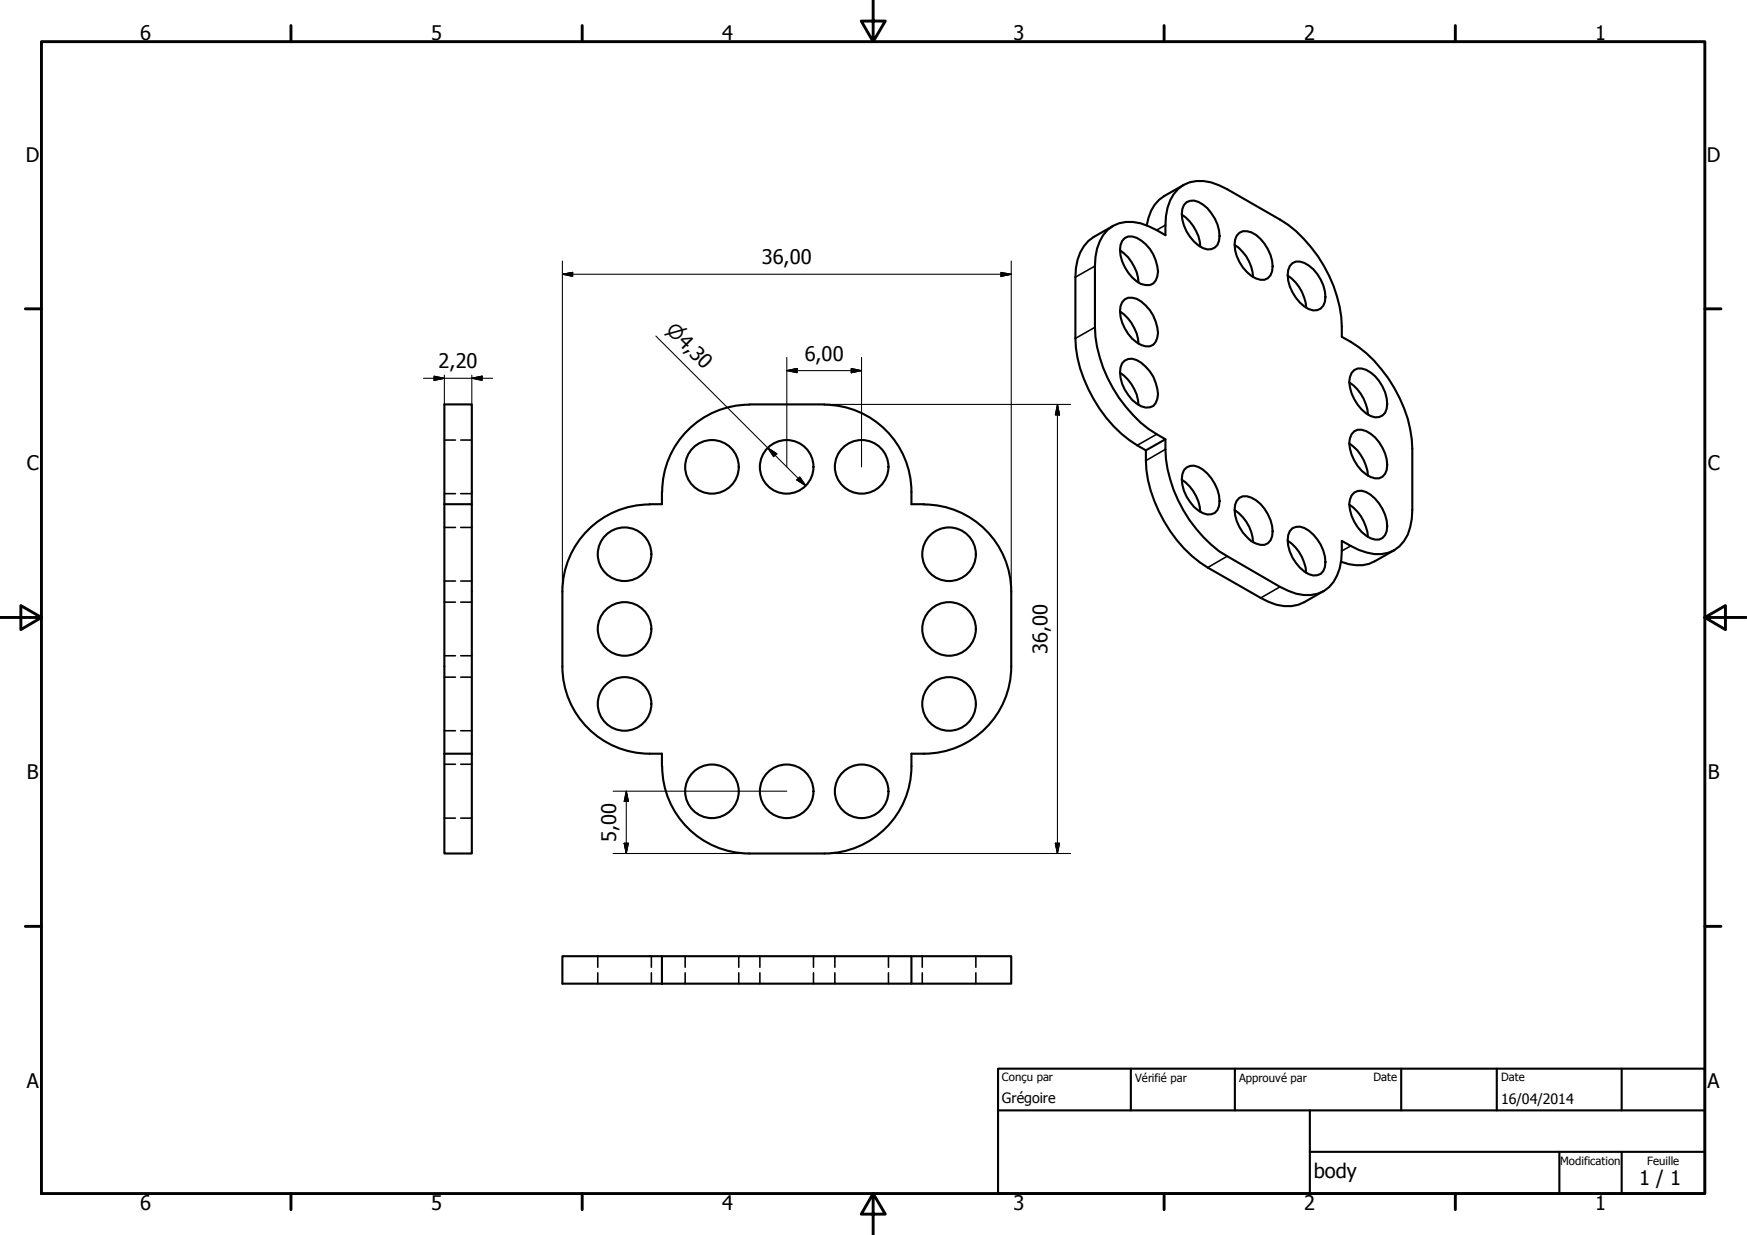
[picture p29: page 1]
body; Grpgoire; Conou par; Vprifip par; Approuvp par; Date; Modification; Feuille

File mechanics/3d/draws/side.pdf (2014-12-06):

1

2

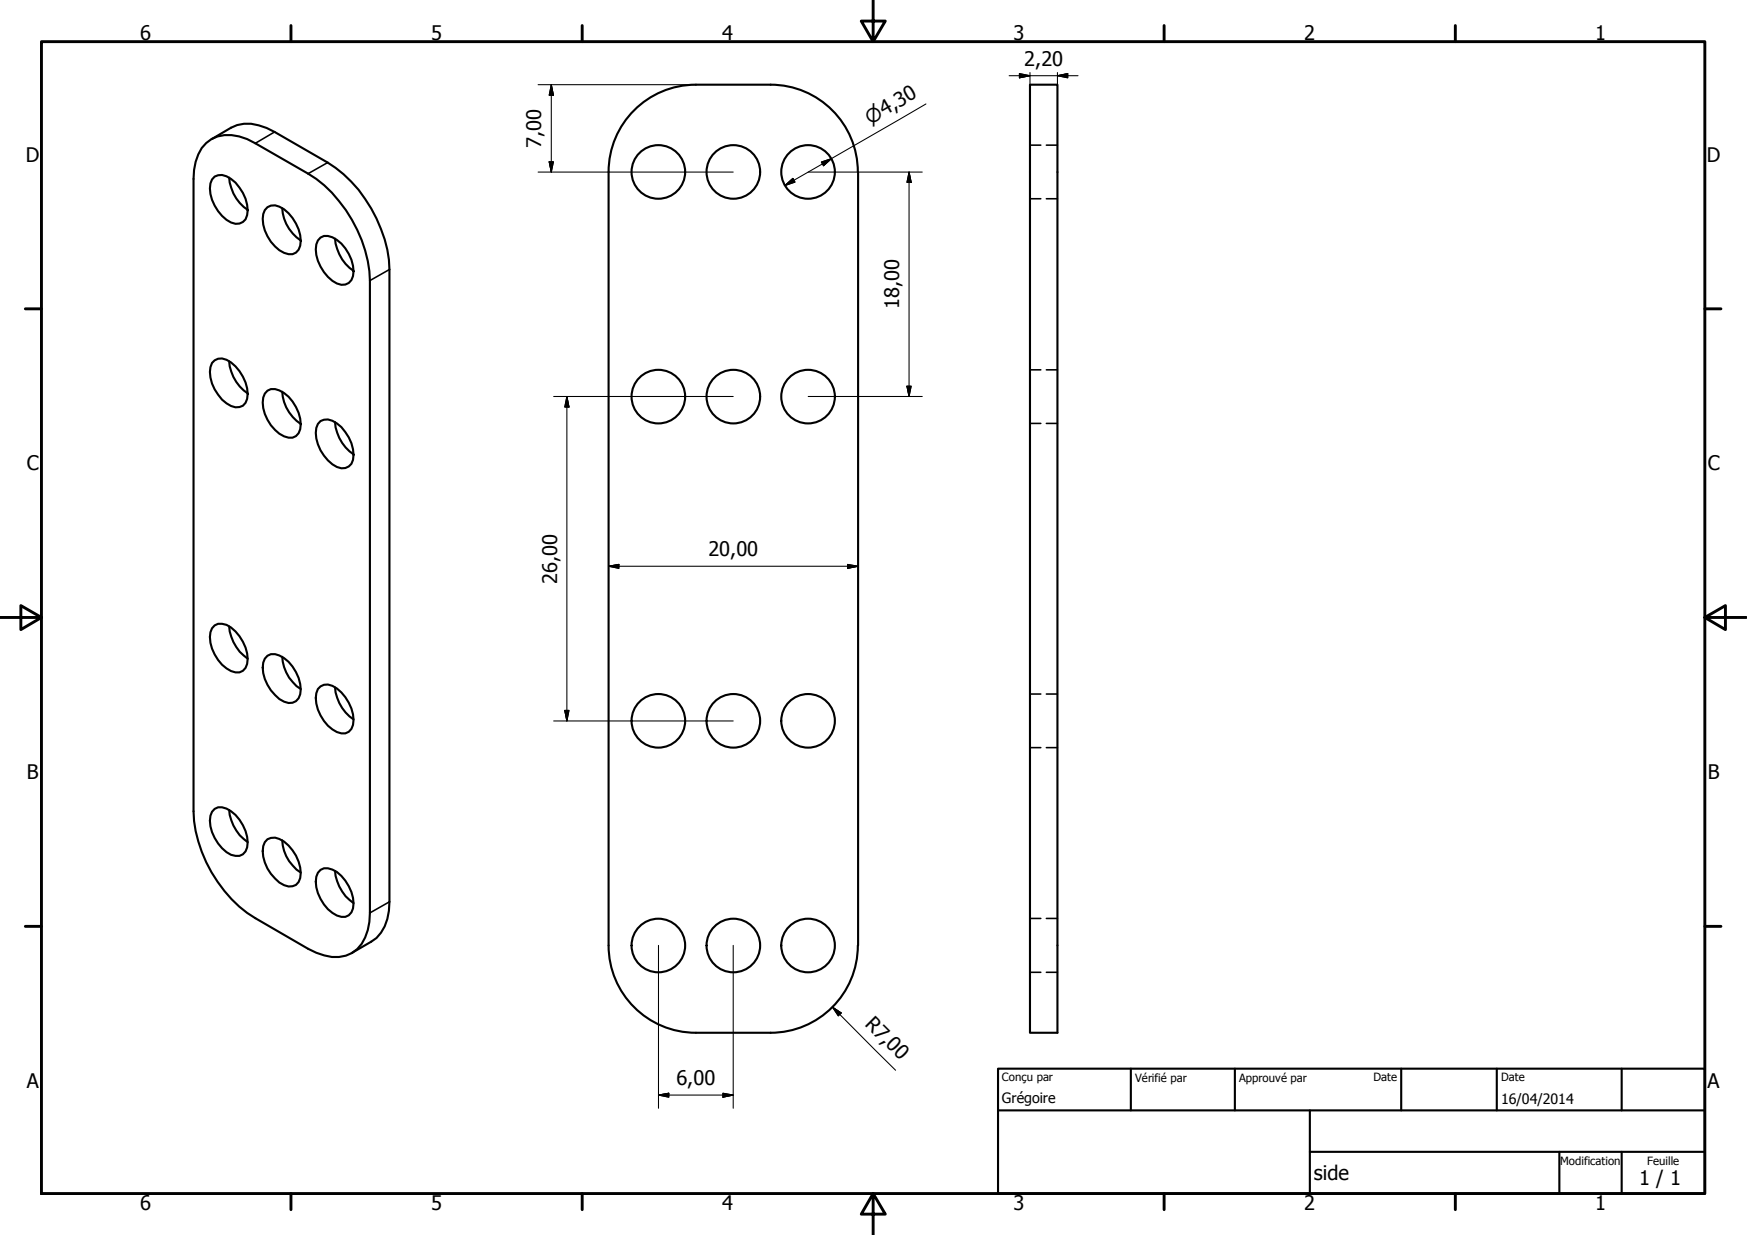
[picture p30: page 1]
side; Grpgoire; Conou par; Vprifip par; Approuvp par; Date; Modification; Feuille

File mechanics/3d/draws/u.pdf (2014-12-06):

1

2

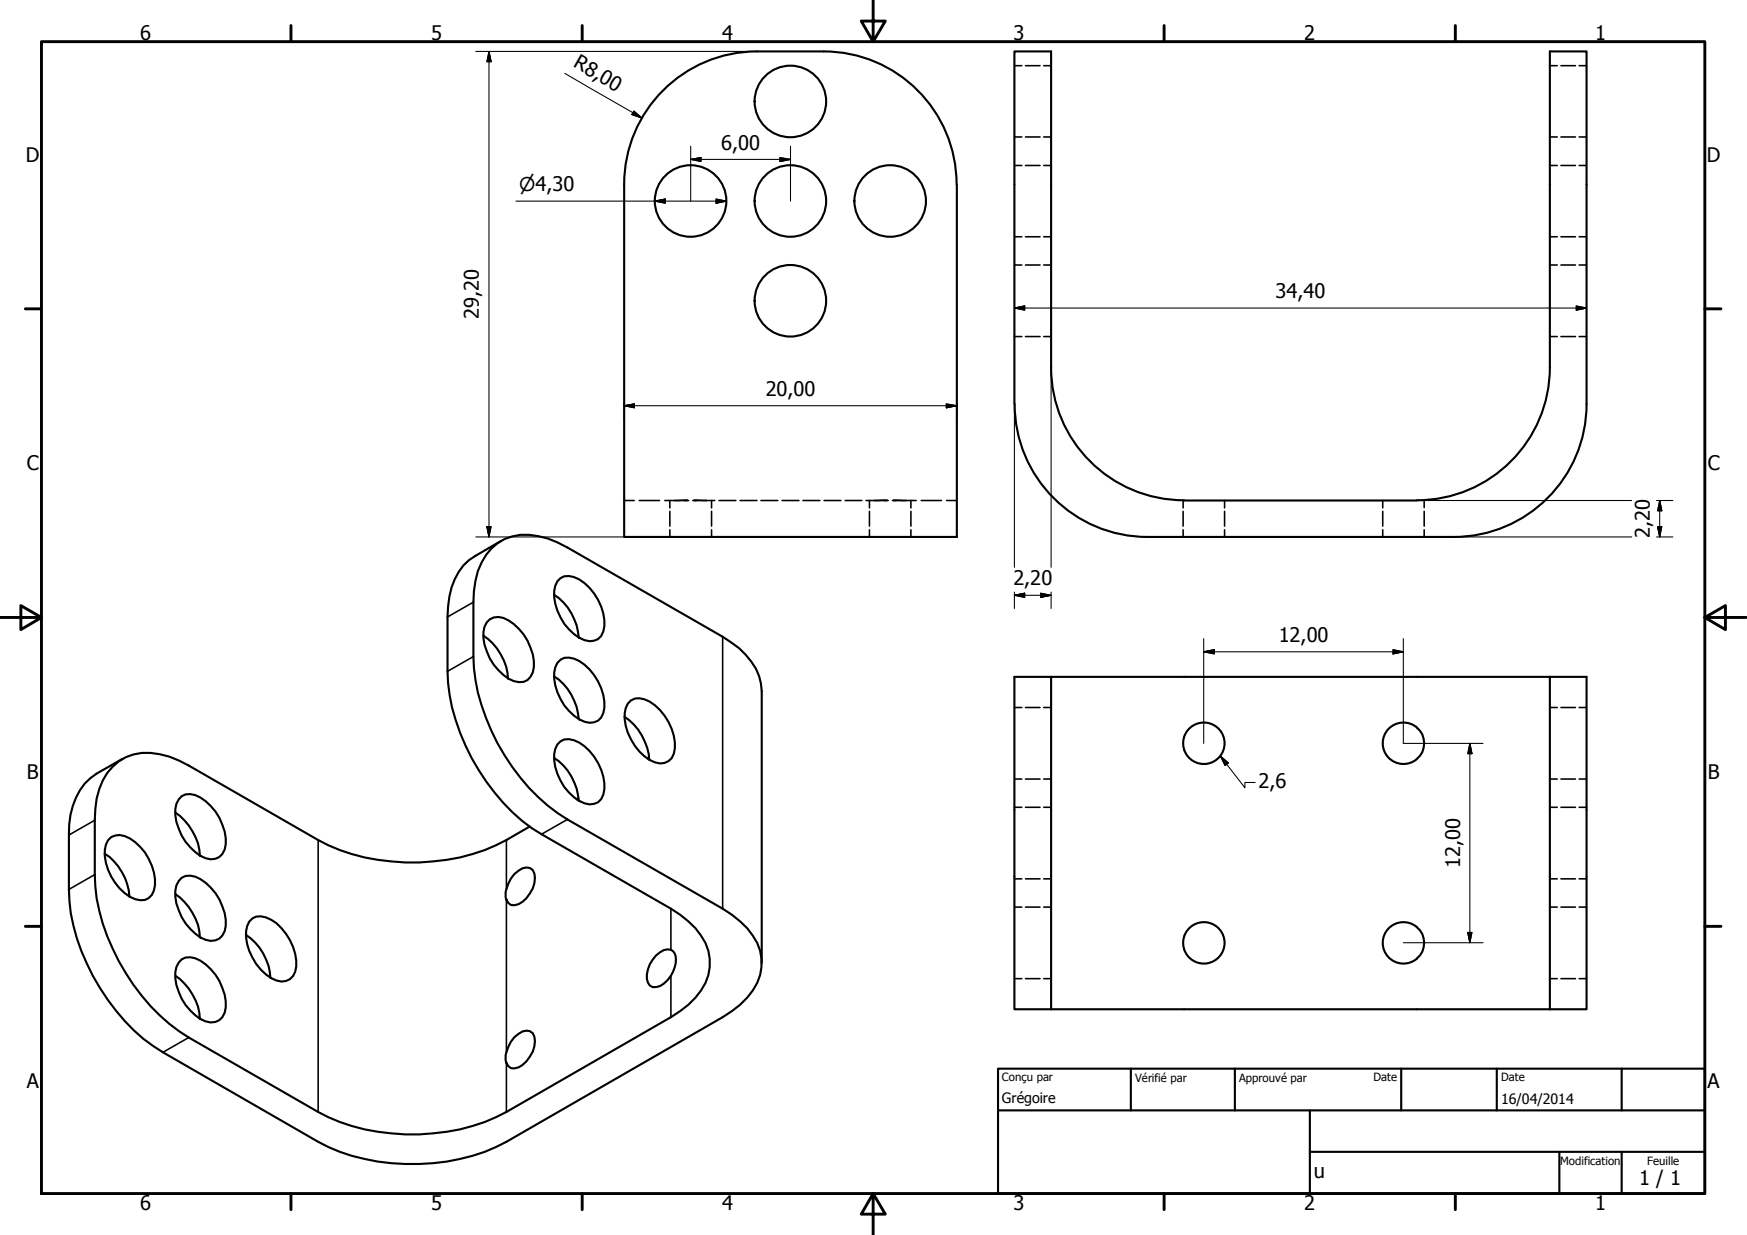
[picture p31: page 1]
Grpgoire; Conou par; Vprifip par; Approuvp par; Date; Modification; Feuille

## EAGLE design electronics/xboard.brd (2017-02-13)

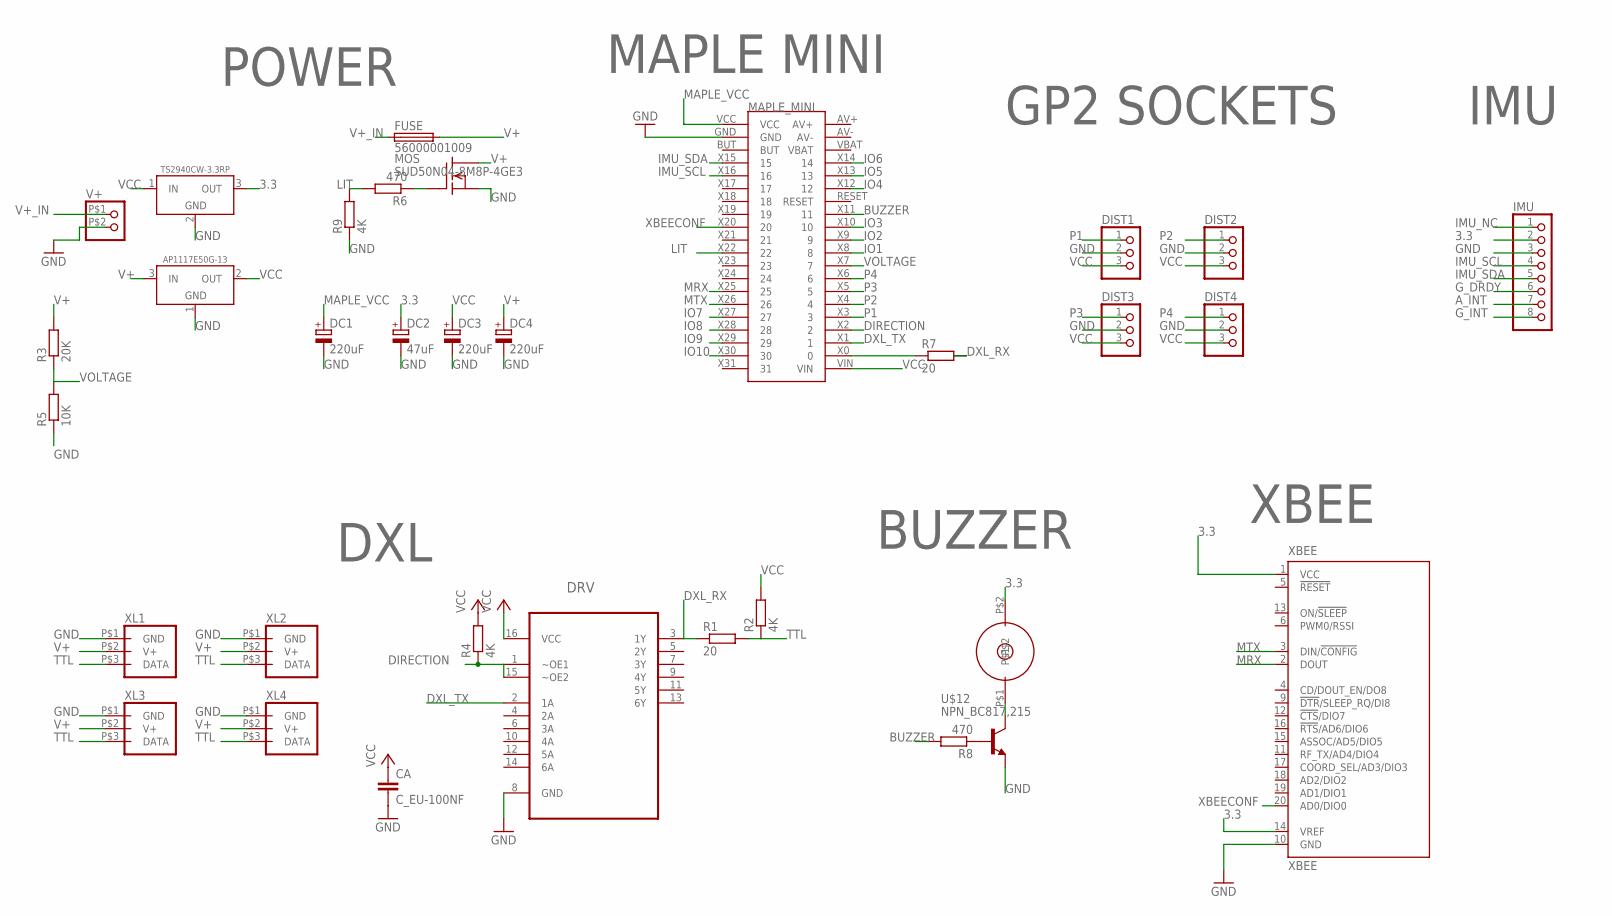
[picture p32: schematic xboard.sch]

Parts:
BUZZER: BUZZER66
CA: C_EU-100NF; C0805
DC1, DC3, DC4: 220uF; PANASONIC_D8
DC2: 47uF; PANASONIC_D
DIST1, DIST2, DIST3, DIST4: CONNEC_1X03
DRV: CD74HCT367M; SOIC127P600X175-16N
FUSE: 56000001009
IMU: CONNEC_1X08
MAPLE_MINI: MAPLE_MINI; CONNEC_2X20
MOS: SUD50N04-8M8P-4GE3; TO252
R1, R7: 20; R0805
R2, R4, R9: 4K; R0805
R3: 20K; R0805
R5: 10K; R0805
R6, R8: 470; R0805
U$7: TS2940CW-3.3RP; SOT223
U$8: AP1117E50G-13; SOT223
U$12: NPN_BC817,215; SOT-23
V+: CONNEC_1X02BIG; CONNEC_1X02_BIG
XBEE: XBEE
XL1, XL2, XL3, XL4: XL_320_CONNEC; DXL_320_CONNEC

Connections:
3.3: BUZZER.P$2, DC2.+, IMU.2, U$7.3 (OUT), XBEE.1 (VCC), XBEE.14 (VREF)
A_INT: IMU.7
BUZZER: MAPLE_MINI.X11 (11), R8.2
DIRECTION: DRV.1 (~OE1), DRV.15 (~OE2), MAPLE_MINI.X2 (2), R4.1
DXL_RX: DRV.3 (1Y), R1.1, R7.2
DXL_TX: DRV.2 (1A), MAPLE_MINI.X1 (1)
GND: CA.2, DC1.-, DC2.-, DC3.-, DC4.-, DIST1.2, DIST2.2, DIST3.2, DIST4.2, DRV.8 (GND), IMU.3, MAPLE_MINI.GND, MOS.2 (S), R5.1, R9.1, U$7.2 (GND), U$8.1 (GND), U$12.2 (E), V+.P$2 (2), XBEE.10 (GND), XL1.P$1 (GND), XL2.P$1 (GND), XL3.P$1 (GND), XL4.P$1 (GND)
G_DRDY: IMU.6
G_INT: IMU.8
IMU_NC: IMU.1
IMU_SCL: IMU.4, MAPLE_MINI.X16 (16)
IMU_SDA: IMU.5, MAPLE_MINI.X15 (15)
IO1: MAPLE_MINI.X8 (8)
IO2: MAPLE_MINI.X9 (9)
IO3: MAPLE_MINI.X10 (10)
IO4: MAPLE_MINI.X12 (12)
IO5: MAPLE_MINI.X13 (13)
IO6: MAPLE_MINI.X14 (14)
IO7: MAPLE_MINI.X27 (27)
IO8: MAPLE_MINI.X28 (28)
IO9: MAPLE_MINI.X29 (29)
IO10: MAPLE_MINI.X30 (30)
LIT: MAPLE_MINI.X22 (22), R6.2, R9.2
MAPLE_VCC: DC1.+, MAPLE_MINI.VCC
MRX: MAPLE_MINI.X25 (25), XBEE.2 (DOUT)
MTX: MAPLE_MINI.X26 (26), XBEE.3 (DIN/!CONFIG)
unnamed: MOS.1 (G), R6.1
unnamed: MAPLE_MINI.X0 (0), R7.1
unnamed: R8.1, U$12.1 (B)
unnamed: BUZZER.P$1, U$12.3 (C)
P1: DIST1.1, MAPLE_MINI.X3 (3)
P2: DIST2.1, MAPLE_MINI.X4 (4)
P3: DIST3.1, MAPLE_MINI.X5 (5)
P4: DIST4.1, MAPLE_MINI.X6 (6)
TTL: R1.2, R2.1, XL1.P$3 (DATA), XL2.P$3 (DATA), XL3.P$3 (DATA), XL4.P$3 (DATA)
V+: DC4.+, FUSE.P$2 (2), MOS.3 (D), R3.2, U$8.3 (IN), XL1.P$2 (V+), XL2.P$2 (V+), XL3.P$2 (V+), XL4.P$2 (V+)
V+_IN: FUSE.P$1 (1), V+.P$1 (1)
VCC: CA.1, DC3.+, DIST1.3, DIST2.3, DIST3.3, DIST4.3, DRV.16 (VCC), MAPLE_MINI.VIN, R2.2, R4.2, U$7.1 (IN), U$8.2 (OUT)
VOLTAGE: MAPLE_MINI.X7 (7), R3.1, R5.2
XBEECONF: MAPLE_MINI.X20 (20), XBEE.20 (AD0/DIO0)

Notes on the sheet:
MAPLE MINI
GP2 SOCKETS
XBEE
DXL
POWER
IMU
BUZZER

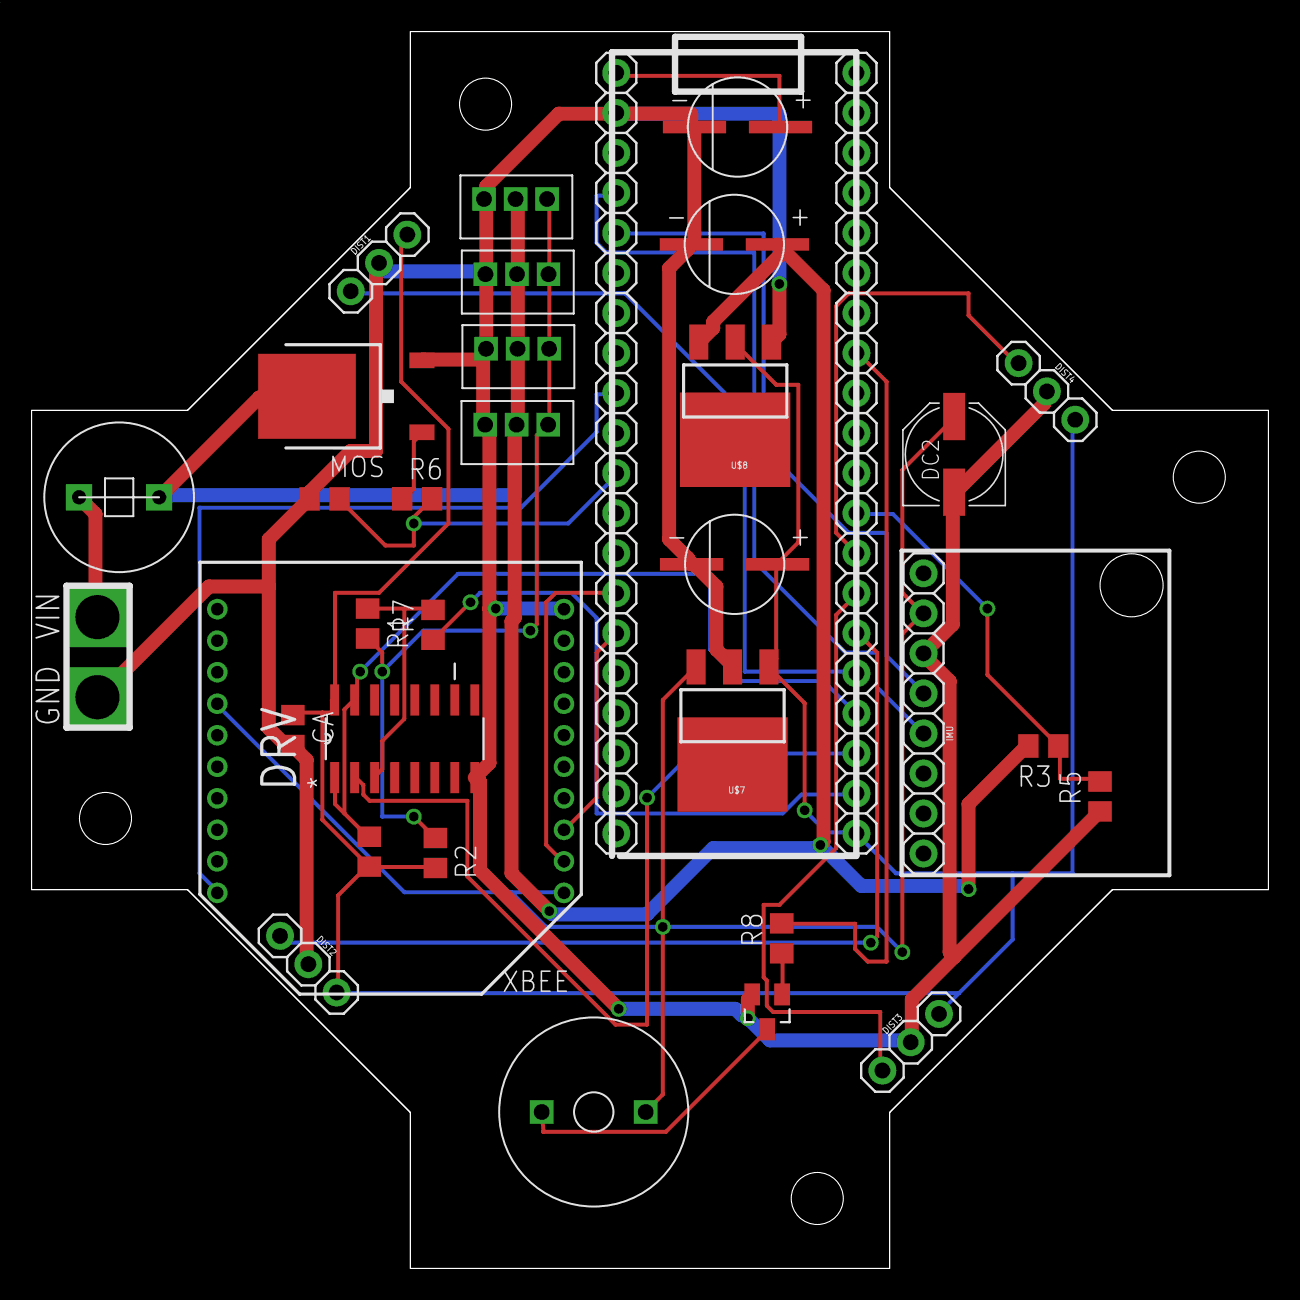
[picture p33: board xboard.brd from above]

Board: 2 copper layers, 78.5 x 78.5 mm, 37 parts (0 on the bottom side), 26 nets.

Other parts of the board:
U$1, U$2, U$3, U$4: STAND-OFF

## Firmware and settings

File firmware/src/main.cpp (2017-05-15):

#include <stdlib.h>
#include <wirish/wirish.h>
#include <servos.h>
#include <terminal.h>
#include <main.h>
#include <math.h>
#include <dxl.h>
#include <function.h>
#include <commands.h>
#include <rc.h>
#include <rhock.h>
#include "motors.h"
#include "voltage.h"
#include "buzzer.h"
#include "distance.h"
#include "config.h"
#include "motion.h"
#include "leds.h"
#include "mapping.h"
#include "behavior.h"
#include "imu.h"
#include "bt.h"

bool isUSB = false;

// Time
TERMINAL_PARAMETER_FLOAT(t, "Time", 0.0);

TERMINAL_COMMAND(version, "Getting firmware version")
{
    terminal_io()->print("version=");
    terminal_io()->println(METABOT_VERSION);
}

TERMINAL_COMMAND(started, "Is the robot started?")
{
    terminal_io()->print("started=");
    terminal_io()->println(started);
}

TERMINAL_COMMAND(rc, "Go to RC mode")
{
    RC.begin(BT_BAUD);
    terminal_init(&RC);
    isUSB = false;
}

// Enabling/disabling move
TERMINAL_PARAMETER_BOOL(move, "Enable/Disable move", true);

// This destroys the fuse (used in dev)
/*
TERMINAL_COMMAND(suicide, "Lit the fuse")
{
    digitalWrite(LIT, HIGH);
}
*/

// Setting the flag, called @50hz
bool flag = false;
void setFlag()
{
    flag = true;
}

/**
 * Checks wether there is enough voltage to start the motors
 */
bool can_start()
{
    if (voltage_current() < 6 || voltage_error()) {
        buzzer_play(MELODY_WARNING);
        return false;
    }

    return true;
}

/**
 * Initializing
 */
void setup()
{
    // Input button
    pinMode(BOARD_BUTTON_PIN, INPUT);

    // Initializing terminal on the RC port
    RC.begin(BT_BAUD);
    terminal_init(&RC);

    // Lit pin is output low
    digitalWrite(LIT, LOW);
    pinMode(LIT, OUTPUT);

    // Initializing bluetooth module
    bt_init();

    // Initializing
    motion_init();

    // Initializing voltage measurement
    voltage_init();

    // Initializing the DXL bus
    delay(500);
    dxl_init();

    // Initializing config (see config.h)
    config_init();

    // initializing distance
    distance_init();

    // Initializing the IMU
    imu_init();

    // Initializing positions to 0
    for (int i=0; i<12; i++) {
        dxl_set_position(i+1, 0.0);
    }
    for (int i=0; i<4; i++) {
        l1[i] = l2[i] = l3[i] = 0;
    }

    // Configuring board LED as output
    pinMode(BOARD_LED_PIN, OUTPUT);
    digitalWrite(BOARD_LED_PIN, LOW);

    // Initializing the buzzer, and playing the start-up melody
    buzzer_init();
    buzzer_play(MELODY_BOOT);

    // Enable 50hz ticking
    servos_init();
    servos_attach_interrupt(setFlag);

    RC.begin(BT_BAUD);
}

/**
 * Computing the servo values
 */
void tick()
{
    static bool wasMoving = false;

    if (voltage_error()) {
        // If there is a voltage error, blinks the LEDs orange and
        // stop any motor activity
        dxl_disable_all();
#ifdef RHOCK
        rhock_killall();
#endif
        if (t < 0.5) {
            led_set_all(LED_R|LED_G);
        } else {
            led_set_all(0);
        }
        t += 0.02;
        if (t > 1.0) t -= 1.0;
        return;
    }

    // The robot is disabled
    if (!move || !started) {
        motors_read();
        t = 0.0;
        return;
    }

    // Incrementing and normalizing t
    t += motion_get_f()*0.02;
    if (t > 1.0) {
        t -= 1.0;
        colorize();
    }
    if (t < 0.0) t += 1.0;

    if (!wasMoving && motion_is_moving()) {
        t = 0.0;
    }
    wasMoving = motion_is_moving();

    // Robot behavior
    behavior_tick(0.02);

    motion_tick(t);

    // Sending order to servos
    dxl_set_position(mapping[0], l1[0]);
    dxl_set_position(mapping[3], l1[1]);
    dxl_set_position(mapping[6], l1[2]);
    dxl_set_position(mapping[9], l1[3]);

    dxl_set_position(mapping[1], l2[0]);
    dxl_set_position(mapping[4], l2[1]);
    dxl_set_position(mapping[7], l2[2]);
    dxl_set_position(mapping[10], l2[3]);

    dxl_set_position(mapping[2], l3[0]);
    dxl_set_position(mapping[5], l3[1]);
    dxl_set_position(mapping[8], l3[2]);
    dxl_set_position(mapping[11], l3[3]);
}

static int btnLast = 0;
static bool btn = false;
static int id = 13;

void buttonPress()
{
    btnLast = millis();
}

void idAudio()
{
    for (int k=0; k<id; k++) {
        buzzer_beep(400, 50);
        buzzer_wait_play();
        delay(150);
    }
}

/**
 * The button is used to do some configurations, for more information
 * please refer to the official documentation
 */
void buttonRelease()
{
    if (millis()-btnLast > 6000) {
        // Pressed more than 6s, configuring bluetooth
        buzzer_play(MELODY_BEGIN);
        buzzer_wait_play();
        bt_set_config("Metabot", "1234");
        buzzer_play(MELODY_BEGIN);
        buzzer_wait_play();
    } else if (millis()-btnLast > 2000) {
        // Pressed more than 2s, entering ID sequence
        id = 1;
        buzzer_play(MELODY_BEGIN);
        buzzer_wait_play();
    } else {
        // Next id sequence
        if (id <= 12) {
            int success = 0;

            // Checking that there is exactly one servo on the bus
            int discover = 0;
            for (int k=1; k<=12; k++) {
                bool ok = false;
                for (int t=0; t<3; t++) {
                    if (dxl_ping(k)) {
                        ok = true;
                    }
                    delay(3);
                }
                if (ok) {
                    discover++;
                }
            }

            // Configuring the servo on the bus to the target ID
            // (using broadcast as address)
            if (discover == 1) {
                for (int k=0; k<3; k++) {
                    dxl_configure(DXL_BROADCAST, id);
                    dxl_write_byte(id, DXL_LED, LED_G);
                    delay(30);
                    // Checking that the servo now is correct
                    if (dxl_ping(id)) {
                        success++;
                    }
                }
            }

            // Next ID
            if (success > 0) {
                idAudio();
                id++;

                if (id > 12) {
                    // It's over
                    delay(500);
                    buzzer_play(MELODY_BEGIN);
                    buzzer_wait_play();
                }
            } else {
                buzzer_play(MELODY_WARNING);
                buzzer_wait_play();
            }
        }
    }
}

void loop()
{
    bool btnNew = digitalRead(BOARD_BUTTON_PIN);
    if (btnNew != btn) {
        if (btnNew) buttonPress();
        else buttonRelease();
        btn = btnNew;
    }

    // Buzzer update
    buzzer_tick();
    // IMU ticking
    imu_tick();
    // Sampling the voltage
    voltage_tick();
    // Sampling the distance
    distance_tick();

    // Updating the terminal
    terminal_tick();
#if defined(RHOCK)
    rhock_tick();
#endif
    if (SerialUSB.available() && !isUSB) {
        isUSB = true;
        terminal_init(&SerialUSB);
    }
    if (RC.available() && isUSB) {
        isUSB = false;
        terminal_init(&RC);
    }

    // Calling user motion tick
    if (flag) {
        flag = false;
        tick();
        dxl_flush();
    }
}

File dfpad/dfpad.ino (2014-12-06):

#include "buttons.h"
#include "com.h"

// Height and front correction
#define DEFAULT_H  -70
#define DEFAULT_FH 0

int cheat = 0;
int safe = 1;
float h = DEFAULT_H;
float frontH = DEFAULT_FH;

// Remapping
int remap = 0;

// Is the robot started?
bool started = false;

// Crab mode?
bool crab = false;

// Using legs backward?
bool backLegs = false;

void setup() {
  initButtons();
  initCom(); 
  
  struct state btns = readButtons();
  if (btns.select) {
    safe = 0;
  }  
}

void loop() {
  comTick();
  struct state btns = readButtons();

  ON_RELEASE(start) {
    started = !started; 
    if (started) {
      command("start");
    } 
    else {
      command("stop");
    }
  }

  ON_CHANGE(joypad_left_x) { 
    command("dx", -normalize(btns.joypad_left_x));
  }

  ON_CHANGE(joypad_left_y) {
    command("dy", normalize(btns.joypad_left_y));    
  }

  ON_CHANGE(joypad_right_y) {
    command("turn", normalize(btns.joypad_right_y)/2.0);    
  }


  if (safe == 0) {
      
    ON_RELEASE(r3) {
      crab = !crab;
      if (crab) {
        command("crab", 30);
      } else {
        command("crab", 0);
      }
    }
    
    ON_RELEASE(r2) {
      backLegs = !backLegs;
      if (backLegs) {
        command("backLegs", 1);
      } else {
        command("backLegs", 0);
      }
    }
  
    ON_RELEASE(select) {
     h = DEFAULT_H;
     frontH = DEFAULT_FH;
     command("h", h);
     command("frontH", frontH);
    }
    
    ON_RELEASE(up) {
      h -= 2;
     command("h", h);    
    }
    ON_RELEASE(down) {
      h += 2;
     command("h", h);    
    }
    ON_RELEASE(left) {
     frontH -= 2;
      command("frontH", frontH);
    }
    ON_RELEASE(right) {
      frontH += 2;
      command("frontH", frontH);
    }
    
    ON_PRESS(lz2) {
      command("alt", 30);
    }
    ON_RELEASE(lz2) {
      command("alt", 15);
    }
    
    ON_PRESS(rz2) {
      command("freq", 0.33);
    }
    ON_RELEASE(rz2) {
      command("freq", 2.0);
    }
    
    ON_RELEASE(lz1) {
      remap++;
      if (remap >= 4) remap = 0;
      command("remap", remap);
    }
    ON_RELEASE(rz1) {
      remap--;
      if (remap < 0) remap = 3;
      command("remap", remap);
    }
  }
  
  last_btns = btns;

  delay(3);
}

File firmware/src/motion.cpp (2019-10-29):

#include <stdio.h>
#include <math.h>
#ifdef HAS_TERMINAL
#include <terminal.h>
#else
#define TERMINAL_PARAMETER_BOOL(name, desc, def) \
    bool name = def;
#define TERMINAL_PARAMETER_FLOAT(name, desc, def) \
    float name = def;
#define TERMINAL_PARAMETER_DOUBLE(name, desc, def) \
    double name = def;
#define TERMINAL_PARAMETER_INT(name, desc, def) \
    int name = def;
#endif
#ifdef __EMSCRIPTEN__
#include <emscripten/bind.h>
#else
#include "imu.h"
#include "voltage.h"
#include "distance.h"
#endif
#ifdef RHOCK
#include <rhock/event.h>
#include <rhock/stream.h>
#endif
#include "config.h"
#include "cubic.h"
#include "motion.h"
#include "kinematic.h"
#include "mapping.h"
#include "leds.h"
#include "motors.h"

// Angles for the legs motor
float l1[4], l2[4], l3[4];

// Extra angles
float a1[4], a2[4], a3[4];

// Extra x, y and z for each leg
static float ex[4], ey[4], ez[4];

float motion_get_motor(int idx)
{
    int c = (idx%3);
    switch (c) {
        case 0:
            return (l1[idx/3]);
            break;
        case 1:
            return (l2[idx/3]);
            break;
        case 2:
            return (l3[idx/3]);
            break;
    }

    return 0;
}

// Amplitude multiplier
#define AMPLITUDE 30

// Speed factor
TERMINAL_PARAMETER_FLOAT(freq, "Time factor gain", 2.0);

// Legs bacakward mode
TERMINAL_PARAMETER_BOOL(backLegs, "Legs backwards", false);

// Amplitude & altitude of the robot
TERMINAL_PARAMETER_FLOAT(alt, "Height of the steps", 22.0);

// Static position
TERMINAL_PARAMETER_FLOAT(r, "Robot size", 153.0);
TERMINAL_PARAMETER_FLOAT(h, "Robot height", -55.0);

// Direction vector
TERMINAL_PARAMETER_FLOAT(dx, "Dx", 0.0);
TERMINAL_PARAMETER_FLOAT(dy, "Dy", 0.0);

// Turning, in ° per step
TERMINAL_PARAMETER_FLOAT(turn, "Turn", 0.0);

// Crab
TERMINAL_PARAMETER_FLOAT(crab, "Crab", 0.0);

// Front delta h
TERMINAL_PARAMETER_FLOAT(frontH, "Front delta H", 0.0);

#ifdef HAS_TERMINAL
TERMINAL_COMMAND(toggleBackLegs, "Toggle back legs")
{
    if (backLegs == 0) backLegs = 1;
    else if (backLegs == 1) backLegs = 0;
}

TERMINAL_COMMAND(toggleCrab, "Toggle crab mode")
{
    if (crab == 0) crab = 30;
    else if (crab == 30) crab = 0;
}
#endif

// Gait selector
TERMINAL_PARAMETER_FLOAT(gait, "Gait", 1);

// Support
float support = 0.5;

// Functions
Cubic rise;
Cubic step;

/**
 * Initializing functions
 */
void setup_functions()
{
    rise.clear();
    step.clear();

    step.addPoint(0, 0.5, 0);
    step.addPoint(support, -0.5, 0);
    step.addPoint(support+(1-support)/2, 0, 1);
    step.addPoint(1, 0.5, 0);

    rise.addPoint(0, 0, 0);
    rise.addPoint(support, 0, 0);
    rise.addPoint(support+(1-support)/2, 1, 0);
    rise.addPoint(1, 0, 0);
}

#ifdef HAS_TERMINAL
TERMINAL_COMMAND(support, "Setup functions")
{
    if (argc == 1) {
        support = atof(argv[0]);
        setup_functions();
    } else {
        terminal_io()->println("Usage: support [duty]");
    }
}
#endif

TERMINAL_PARAMETER_FLOAT(smoothBackLegs, "Smooth 180", 0.0);

// Extra values
float extra_h = 0;
float extra_r = 0;

// Is the robot moving?
bool motion_is_moving()
{
    return (fabs(dx)>0.5 || fabs(dy)>0.5 || fabs(turn)>5);
}

void motion_init()
{
    // Setting the mapping to 0
    remap(0);

    for (int i=0; i<4; i++) {
        ex[i] = 0;
        ey[i] = 0;
        ez[i] = 0;
        a1[i] = 0;
        a2[i] = 0;
        a3[i] = 0;
    }

    extra_h = 0;
    extra_r = 0;
    freq = 2.0;
}

void motion_tick(float t)
{
    if (!motors_enabled()) {
        return;
    }

    // Setting up functions
    setup_functions();

    // Smoothing 180
    if (backLegs && smoothBackLegs < 1) {
        smoothBackLegs += 0.02;
    }
    if (!backLegs && smoothBackLegs > 0) {
        smoothBackLegs -= 0.02;
    }

    float crabRad;
    float phasesA[] = {0.0, 0.5, 1-1e-6, 0.5};
    float phasesB[] = {0.0, 0.5, 0.75, 0.25};

    for (int i=0; i<4; i++) {
        // Defining in which group of opposite legs this leg is
        bool group = ((i&1)==1);

        // This defines the phase of the gait
        float legPhase;

        // Defining gait
        legPhase = t + phasesA[i]*gait + phasesB[i]*(1-gait);

        // Leg target
        float x, y, z, a, b, c;

        // Computing the order in the referencial of the body
        float stepping = step.getMod(legPhase);

        // Add the radius to the leg, in the right direction
        float radius = (r+extra_r);

        // The leg position in the body frame
        float X = (cos(M_PI/4)*radius) * ((i==0||i==1) ? 1 : -1);
        float Y = (cos(M_PI/4)*radius) * ((i==0||i==3) ? 1 : -1);
        float X_ = X;
        float Y_ = Y;

        // Applying crab
        crabRad = DEG2RAD(crab) * (group ? 1 : -1);
        X = cos(crabRad)*X_ - sin(crabRad)*Y_;
        Y = sin(crabRad)*X_ + cos(crabRad)*Y_;

        // Extras
        X += ex[i];
        Y += ey[i];

        // Add dX and dY to the moving vector
        if (fabs(turn) > 0.5) {
            float turnRad = -DEG2RAD(turn);
            float theta = -stepping*turnRad;
            float l = sqrt(dx*dx+dy*dy)/turnRad;
            float r = atan2(dy, dx);
            float cr = cos(-r);
            float sr = sin(-r);

            X_ = X; Y_ = Y;
            X = X_*cr - Y_*sr;
            Y = X_*sr + Y_*cr;

            X_ = X; Y_ = Y;
            X = X_*cos(theta) - (Y_+l)*sin(theta);
            Y = X_*sin(theta) + (Y_+l)*cos(theta) - l;

            X_ = X; Y_ = Y;
            X = X_*cr - Y_*(-sr);
            Y = X_*(-sr) + Y_*cr;
        } else {
            X += stepping*dx;
            Y += stepping*dy;
        }

        // Move to the leg frame
        float vx, vy;
        legFrame(X, Y, &vx, &vy, i, L0);

        // The robot is moving if there is dynamics parameters
        bool moving = motion_is_moving();

        // This is the x,y,z order in the referencial of the leg
        x = vx;
        y = vy;
        z = ez[i] + h - extra_h + (moving ? (rise.getMod(legPhase)*alt) : 0);
        if (i < 2) z += frontH;

        // Computing inverse kinematics
        if (computeIK(x, y, z, &a, &b, &c, L1, L2, backLegs ? L3_2 : L3_1)) {
            l1[i] = -SIGN_A*a + a1[i];
            l2[i] = -SIGN_B*b + a2[i];
            l3[i] = -SIGN_C*(c - 180*smoothBackLegs) + a3[i];
        }
    }
}

#ifdef __EMSCRIPTEN__
float sim_t = 0.0;
#endif

void motion_reset()
{
    motion_init();

#ifdef __EMSCRIPTEN__
    sim_t = 0.0;
#endif
}

void motion_set_f(float f_)
{
    freq = f_;
}

float motion_get_f()
{
    return freq;
}

void motion_set_h(float h_)
{
    extra_h = h_;
}

void motion_set_r(float r_)
{
    extra_r = r_;
}

void motion_set_x_speed(float x_speed)
{
    dx = ODOMETRY_TRANSLATION*x_speed/(2.0*freq);
}

void motion_set_y_speed(float y_speed)
{
    dy = ODOMETRY_TRANSLATION*y_speed/(2.0*freq);
}

void motion_set_turn_speed(float turn_speed)
{
    turn = ODOMETRY_ROTATION*turn_speed/(2.0*freq);
}
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

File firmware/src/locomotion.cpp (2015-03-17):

#include <stdio.h>
#include <math.h>
#ifdef HAS_TERMINAL
#include <terminal.h>
#else
#define TERMINAL_PARAMETER_BOOL(name, desc, def) \
    bool name = def;
#define TERMINAL_PARAMETER_FLOAT(name, desc, def) \
    float name = def;
#define TERMINAL_PARAMETER_DOUBLE(name, desc, def) \
    double name = def;
#define TERMINAL_PARAMETER_INT(name, desc, def) \
    int name = def;
#endif
#ifdef __EMSCRIPTEN__
#include <emscripten/bind.h>
#endif
#ifdef RHOCK
#include <rhock/event.h>
#include <rhock/stream.h>
#endif
#include "config.h"
#include "function.h"
#include "locomotion.h"
#include "kinematic.h"
#include "mapping.h"
#include "leds.h"

// Angles for the legs motor
float l1[4], l2[4], l3[4];
// Extra x, y and z for each leg
float ex[4], ey[4], ez[4];

float locomotion_get_motor(int idx)
{
    int c = (idx%3);
    switch (c) {
        case 0:
            return DEG2RAD(l1[idx/3]);
            break;
        case 1:
            return DEG2RAD(l2[idx/3]);
            break;
        case 2:
            return DEG2RAD(l3[idx/3]);
            break;
    }

    return 0;
}

// Amplitude multiplier
#define AMPLITUDE 30

// Legs bacakward mode
TERMINAL_PARAMETER_BOOL(backLegs, "Legs backwards", false);

// Body backward mode
TERMINAL_PARAMETER_BOOL(back, "Mode back", false);

// Amplitude & altitude of the robot
TERMINAL_PARAMETER_FLOAT(alt, "Height of the steps", 15.0);

// Static position
TERMINAL_PARAMETER_FLOAT(r, "Robot size", 90.0);
TERMINAL_PARAMETER_FLOAT(h, "Robot height", -55.0);

// Direction vector
TERMINAL_PARAMETER_FLOAT(dx, "Dx", 0.0);
TERMINAL_PARAMETER_FLOAT(dy, "Dy", 0.0);
TERMINAL_PARAMETER_FLOAT(crab, "Crab", 0.0);

// Turning, in ° per step
TERMINAL_PARAMETER_FLOAT(turn, "Turn", 0.0);

// Front delta h
TERMINAL_PARAMETER_FLOAT(frontH, "Front delta H", 0.0);

#ifdef HAS_TERMINAL
TERMINAL_COMMAND(toggleBackLegs, "Toggle back legs")
{
    if (backLegs == 0) backLegs = 1;
    else if (backLegs == 1) backLegs = 0;
}

TERMINAL_COMMAND(toggleCrab, "Toggle crab mode")
{
    if (crab == 0) crab = 30;
    else if (crab == 30) crab = 0;
}
#endif

// Gait selector
#define GAIT_WALK       0
#define GAIT_TROT       1
TERMINAL_PARAMETER_INT(gait, "Gait (0:walk, 1:trot)", GAIT_TROT);

// Functions
Function rise;
Function step;

/**
 * Initializing functions
 */
void setup_functions()
{
    rise.clear();
    step.clear();
    
    if (gait == GAIT_WALK) {
        // Rising the legs
        rise.addPoint(0.0, 0.0);
        rise.addPoint(0.1, 1.0);
        rise.addPoint(0.3, 1.0);
        rise.addPoint(0.35, 0.0);
        rise.addPoint(1.0, 0.0);

        // Taking the leg forward
        step.addPoint(0.0, -0.5);
        step.addPoint(0.12, -0.5);
        step.addPoint(0.3, 0.5);
        step.addPoint(0.35, 0.5);
        step.addPoint(1.0, -0.5);
    }

    if (gait == GAIT_TROT) {
        // Rising the legs
        rise.addPoint(0.0, 0.0);
        rise.addPoint(0.1, 1.0);
        rise.addPoint(0.4, 1.0);
        rise.addPoint(0.5, 0.0);
        rise.addPoint(1.0, 0.0);

        // Taking the leg forward
        step.addPoint(0.0, -0.5);
        step.addPoint(0.1, -0.5);
        step.addPoint(0.4, 0.5);
        step.addPoint(1.0, -0.5);
    }
}

TERMINAL_PARAMETER_FLOAT(smoothBackLegs, "Smooth 180", 0.0);
TERMINAL_PARAMETER_FLOAT(smoothBack, "Smooth Back", -1.0);

// Extra values
float extra_h = 0;

void locomotion_init()
{
    // Setting the mapping to 0
    remap(0);

    // initializing the locomotion variables to default
    back = (initialOrientation != 0);
    if (back) smoothBack = 1;

    for (int i=0; i<4; i++) {
        ex[i] = 0;
        ey[i] = 0;
        ez[i] = 0;
    }

    extra_h = 0;
}

float last_t = 0;
    
void locomotion_tick(float t)
{
    last_t = t;

    // Setting up functions
    setup_functions();

    // Smoothing 180
    if (backLegs && smoothBackLegs < 1) {
        smoothBackLegs += 0.02;
    }
    if (!backLegs && smoothBackLegs > 0) {
        smoothBackLegs -= 0.02;
    }
    if (back && smoothBack < 1) {
        smoothBack += 0.04;
    }
    if (!back && smoothBack > -1) {
        smoothBack -= 0.04;
    }
        
    for (int i=0; i<4; i++) {
        // Defining in which group of opposite legs this leg is
        bool group = ((i&1)==1);

        // This defines the phase of the gait
        float legPhase;
       
        if (gait == GAIT_WALK) {
            float phases[] = {0.0, 0.5, 0.75, 0.25};
            legPhase = t + phases[i];
        }
        if (gait == GAIT_TROT) {
            legPhase = t + group*0.5;
        }

        float x, y, z, a, b, c;

        // Computing the order in the referencial of the body
        float xOrder = step.getMod(legPhase)*dx;
        float yOrder = step.getMod(legPhase)*dy;

        // Computing the order in the referencial of the leg
        float bodyAngle = -(i*M_PI/2.0 - (M_PI/4.0))*smoothBack;
        if (group) {
            bodyAngle -= DEG2RAD(crab*(-smoothBack));
        } else {
            bodyAngle += DEG2RAD(crab*(-smoothBack));
        }
        float vx = xOrder*cos(bodyAngle)-yOrder*sin(bodyAngle);
        float vy = xOrder*sin(bodyAngle)+yOrder*cos(bodyAngle);

        float enableRise = (fabs(dx)>0.5 || fabs(dy)>0.5 || fabs(turn)>5) ? 1 : 0;

        // This is the x,y,z order in the referencial of the leg
        x = ex[i] + r + vx;
        y = ey[i] + vy;
        z = ez[i] + h - extra_h + rise.getMod(legPhase)*alt*enableRise;
        if (i < 2) z += frontH;
    
        // Computing inverse kinematics
        if (computeIK(x, y, z, &a, &b, &c, L1, L2, backLegs ? L3_2 : L3_1)) {
            if (group) {
                a += crab*(-smoothBack);
            } else {
                a -= crab*(-smoothBack);
            }

            l1[i] = signs[0]*smoothBack*(a + step.getMod(legPhase)*turn);
            l2[i] = signs[1]*smoothBack*(b);
            l3[i] = signs[2]*smoothBack*(c - 180*smoothBackLegs);
        }
    }
}

void locomotion_reset()
{
    locomotion_init();
}

void locomotion_set_h(float h_)
{
    extra_h = h_;
}

void locomotion_set_dx(float dx_)
{
    dx = dx_;
}

void locomotion_set_dy(float dy_)
{
    dy = dy_;
}

void locomotion_set_turn(float turn_)
{
    turn = turn_;
}

float locomotion_get_dx()
{
    return dx;
}

float locomotion_get_dy()
{
    return dy;
}

float locomotion_get_turn()
{
    return turn;
}

#ifdef RHOCK
void rhock_on_monitor()
{
    rhock_stream_begin(RHOCK_STREAM_USER);
    rhock_stream_append_int(RHOCK_NUMBER_TO_VALUE(last_t));
    rhock_stream_append_int(RHOCK_NUMBER_TO_VALUE(dx));
    rhock_stream_append_int(RHOCK_NUMBER_TO_VALUE(dy));
    rhock_stream_append_int(RHOCK_NUMBER_TO_VALUE(turn));
    led_stream_state();
    rhock_stream_end();
}
#endif

#ifdef __EMSCRIPTEN__
using namespace emscripten;
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

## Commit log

2014-12-06 Missing utils
    [rounded.scad, screws.scad, thickLine.scad]
2014-12-09 Fix screw bom
2014-12-09 Voltage check
2014-12-11 New battery fixation
    [batfix.stl, body_bottom.stl, body_top.stl]
2014-12-11 Fixing color
    [metabot.scad]
2014-12-11 Changing servoing, white legs
2014-12-11 Fixing body4
    [body4.scad, config.scad]
2014-12-11 Body4 fixed
    [body_bottom.stl, body_top.stl]
2014-12-11 Removing batfix
    [batfix.scad, parts.scad]
2014-12-12 Removing raspberry
    [raspberry.scad]
2014-12-16 Adding voltage as variable
2014-12-20 Adding plater.conf
2014-12-20 Moving to holes of 3 for Us
    [u.stl]
2015-01-27 Bolt trace
    [body4.scad, bolt_trace.scad]
2015-01-27 Nuts traces
    [body4.scad]
2015-01-28 Recompiled parts
    [body_bottom.stl, body_top.stl, leg.stl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]
2015-01-28 Adding 1mm height
    [body4.scad]
2015-01-28 Body top
    [body_top.stl]
2015-03-09 Fixing error in kill
    [main.cpp]
2015-03-09 Reseting terminal on exiting rhock
    [main.cpp]
2015-03-16 Adding leds control and height
2015-03-17 Not calling RESET stream
    [locomotion.cpp, rhock-functions.cpp]
2015-03-18 Fixing motors colorize
2015-04-07 Adding rhock leg led
2015-05-17 Reducing PID P
2015-07-27 Adding IMU
2015-07-27 Adding accelerometer
2015-07-27 Adding distances sensors
2015-07-29 v2 first design
    [board.ipt, charniere.ipt, clapet.ipt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]
2015-07-29 Fixing voltage= for bc, fixing hysteresis
    [voltage.cpp]
2015-07-29 Fixing i2c errors check
    [imu.cpp]
2015-09-27 Removing debug, yaw as a command
2015-11-27 Fixing master to use current Maple
    [main.cpp]
2016-01-20 V2 Mechanics
    [board.ipt, body.ipt, body_to_opencm.ipt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]
2016-02-25 One distance sensor
2016-03-01 Mechanics (wip)
    [body.scad, body4.scad, config.scad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]
2016-03-01 V2 mechanics (wip)
    [body.scad, body4.scad, body_bottom.scad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]
2016-03-01 Mechanics reorganization (laser+3d)
    [arm.ipt, arm.scad, body.idw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]
2016-03-01 Fixing the body 3D
    [body.scad, config.scad, head.scad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]
2016-03-01 Fixing body gp2
    [body.scad]
2016-03-01 Updating STLs
    [body_bottom.stl, body_top.stl, head.stl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]
2016-03-02 Adding IMU calibrate
2016-03-02 volt to centimeter for GP2
2016-03-02 Fixing r for V2
    [motion.cpp]
2016-03-03 Securing voltage alarm from user code
2016-03-03 GP2 fixation, XBoard symetry
    [body_bottom.ipt, body_bottom.stl]
2016-03-03 More robust body top
    [body_top.ipt]
2016-03-08 Reinitializing i2c on error
    [imu.cpp]
2016-04-06 XBoard schematics
    [xboard.brd, xboard.sch]
2016-04-07 Fixing consistency
    [xboard.brd]
2016-04-25 Signal name place
    [xboard.sch]
2016-05-01 Adding laser sizes
2016-07-26 Buzzer 10mm
    [xboard.brd, xboard.sch]
2016-10-29 Config uniformisation
    [config.scad]
2016-11-02 Uniformisation joints
2016-11-02 DXFs, update.sh
    [body_bottom.dxf, body_top.dxf, head.dxf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]
2016-11-02 Fix leg
    [leg.dxf]
2016-11-03 Fixing motion rotation kinematics
    [motion.cpp]
2016-11-17 BOM wip
2016-11-17 Electronics BOM
2016-11-28 Adding odometry calibration defines
2016-11-28 Stopping buzzer on stop
    [rhock-functions.cpp]
2016-11-28 Stopping buzzer on all stop
    [rhock-functions.cpp]
2016-11-28 context controlling buzzer in rhock
    [rhock-functions.cpp]
2016-11-30 Blinking and stopping motors on voltage error
    [main.cpp]
2016-11-30 Reading motors when disabled
2016-11-30 imu with simulation
2016-11-30 Adding can start to prevent USB starting
    [buzzer.cpp, main.cpp]
2016-11-30 Killing user code in c ase of low voltage issue
    [main.cpp, rhock-functions.cpp]
2016-12-02 Laser prototype dimensions
2016-12-02 3D prototypes
2016-12-07 Updating BOM
2017-01-03 Side stronger
    [side.ipt]
2017-01-05 BOM update
2017-02-09 Adding rhock functions, discounted distance, fixig bt mistake
    [main.cpp, motion.cpp, rhock-functions.cpp]
2017-02-09 Adding yaw/pitch/roll and motor controls virtual machine natives
2017-02-13 Process to ID motors w/ button
2017-02-13 Fixing button IDing
2017-02-13 Board image
2017-03-02 Update kinematic.h
    correct thr to the
2017-05-15 Avoiding buzzer stop when stopping rhock programs when battery low
    [buzzer.cpp]
2017-05-15 Moving leg phases outside the for loop
2017-10-02 Robot drawing, cleaning up assembly alignment
    [robot.dwg, robot.iam]

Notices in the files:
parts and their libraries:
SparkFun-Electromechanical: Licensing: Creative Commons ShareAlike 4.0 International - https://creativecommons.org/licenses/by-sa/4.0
